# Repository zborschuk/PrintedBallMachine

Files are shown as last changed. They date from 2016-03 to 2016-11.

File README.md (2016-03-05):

# PrintedBallMachine
A 3d Printed ball machine, hung on pegboard.

The goal of this repo is to demonstrate the specifications of a printed ball machine, composed of interchangeable modules.

Therefore, the biggest component is the ruleset.

The inlet hopper is given as a standalone STL, for use with other graphics programs, as well as the outlets.

Marbles are 5/8" steel ball bearings.  Steel is heavy.

Inlets align on the 1" marks, outlets on the 1/2"; your machine may raise or lower marbles by any 1" increment.  The centerline for all inlets and outlets is 1" from the start of the hanger.

The easiest module is the simple slope, which is included.  I'll be working on a lifter or two next, and will continue to add modules.

Paul

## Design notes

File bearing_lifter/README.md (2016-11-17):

# Bearing Lifter
This is a lifter module, utilizing a print-in-place bearing.

Mechanical Parts:
1 motors
2 M5 screws and nuts for the handle
4 M3 screws to attach the motor
1 M3 screw to attach the guard

Parts to Print:
1 * bl_inlet.stl
1 * bl_outlet.stl
1 * bl_lift_gear.stl
1 * bl_drive_gear.stl
1 * bl_spiral.stl
1 * bl_guard.stl

Standard Parts
2 * stand.stl
1 * handle.stl
1 * breturn_inlet.stl
1 * breturn_outlet.stl
2 * breturn_peg.stl
4 * peg_1x.stl
1 * peg_2x.stl
6 * peg_3x.stl

Notes:
Motor direction matters!
bl_inlet uses long pegs where it can.
You need a sideways support peg for the bl_outlet, under the fang-like curve.

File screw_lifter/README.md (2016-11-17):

# Screw Lifter
This is a lifter module, utilizing two separate screw lifters and a spiral drop.

Mechanical Parts:
2 motors
2 M5 screws and nuts for the handle

Parts to Print:
2 * sl_inlet.stl
2 * sl_screw_2s.stl
1 * sl_bowl_drop.stl
1 * sl_bowl_catch.stl

Standard Parts
2 * stand.stl
1 * handle.stl
1 * breturn_inlet.stl
1 * breturn_outlet.stl
2 * breturn_peg.stl
4 * peg_1x.stl
2 * peg_2x.stl
4 * peg_3x.stl
1 * insert_peg.stl

Notes:
Motor direction matters!
sl_inlet uses long pegs where it can.
sl_bowl_catch.stl needs an insert peg on its outlet.

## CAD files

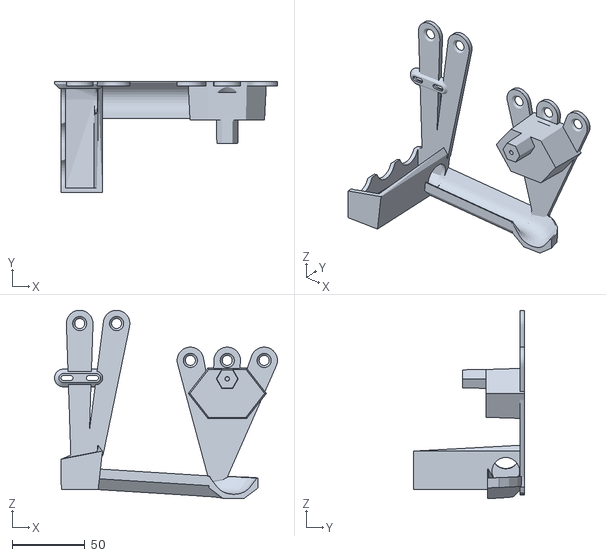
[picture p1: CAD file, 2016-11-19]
bearing_lifter/bl_inlet.stl
153.5 x 76.3 x 129.7

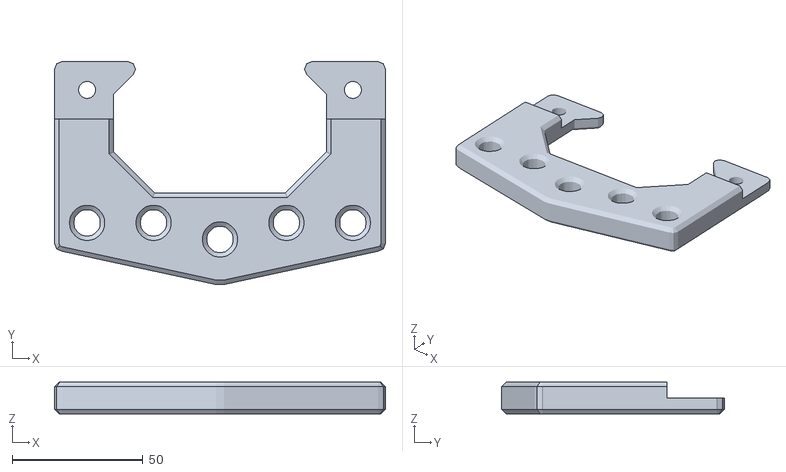
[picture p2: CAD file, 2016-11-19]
bearing_lifter/handle.stl
126.5 x 85.2 x 12.2

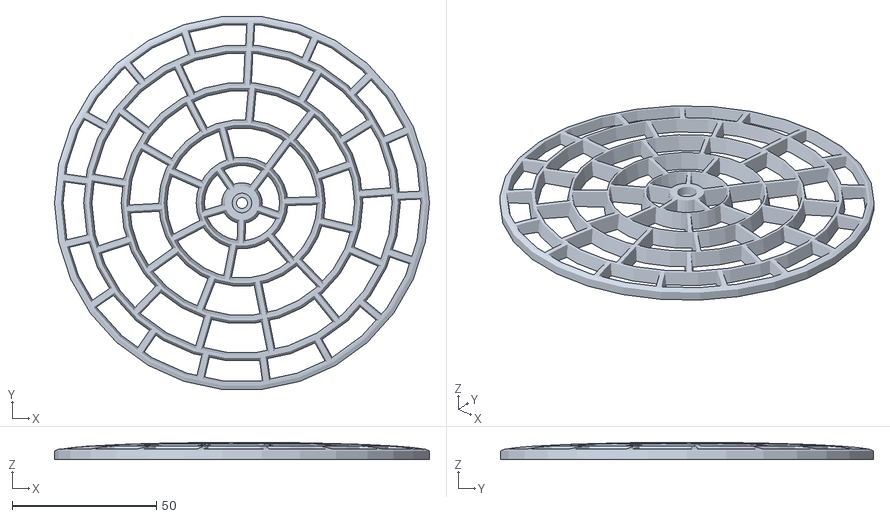
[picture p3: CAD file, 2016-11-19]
bearing_lifter/bl_guard.stl
130.0 x 129.3 x 5.98

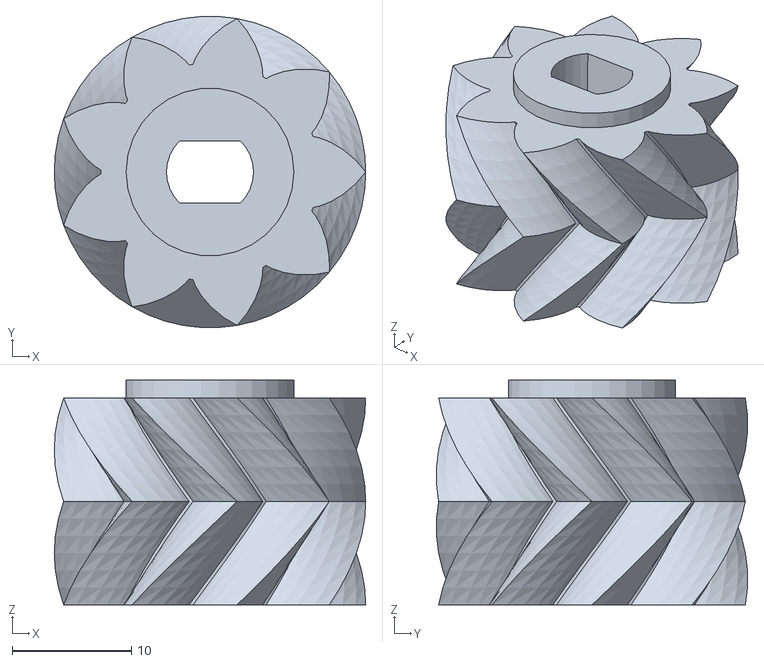
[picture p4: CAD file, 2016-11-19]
bearing_lifter/bl_drive_gear.stl
26.2 x 26.1 x 18.9

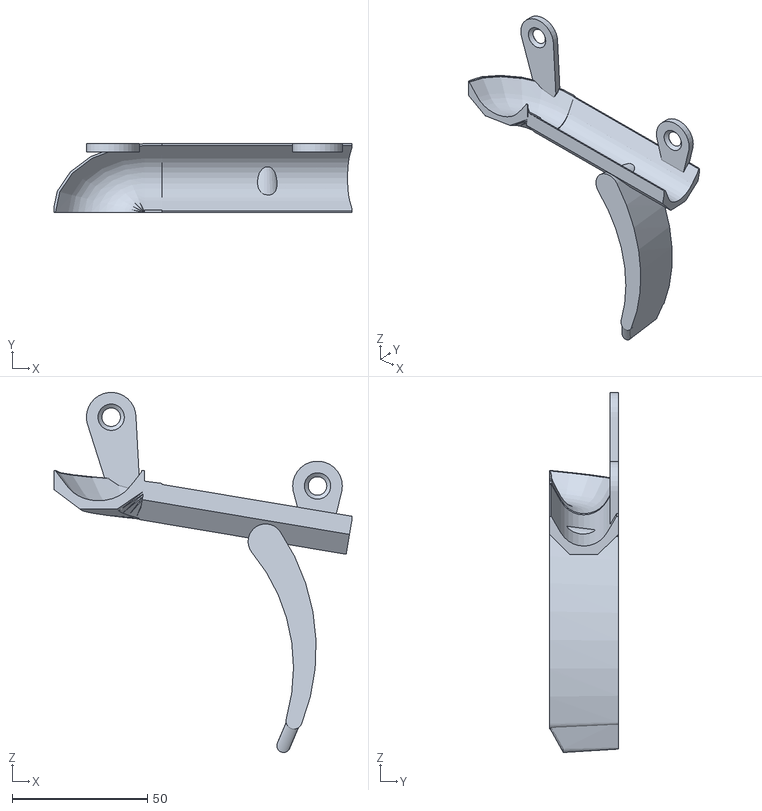
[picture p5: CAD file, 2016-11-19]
bearing_lifter/bl_outlet.stl
110.0 x 25.5 x 133.0

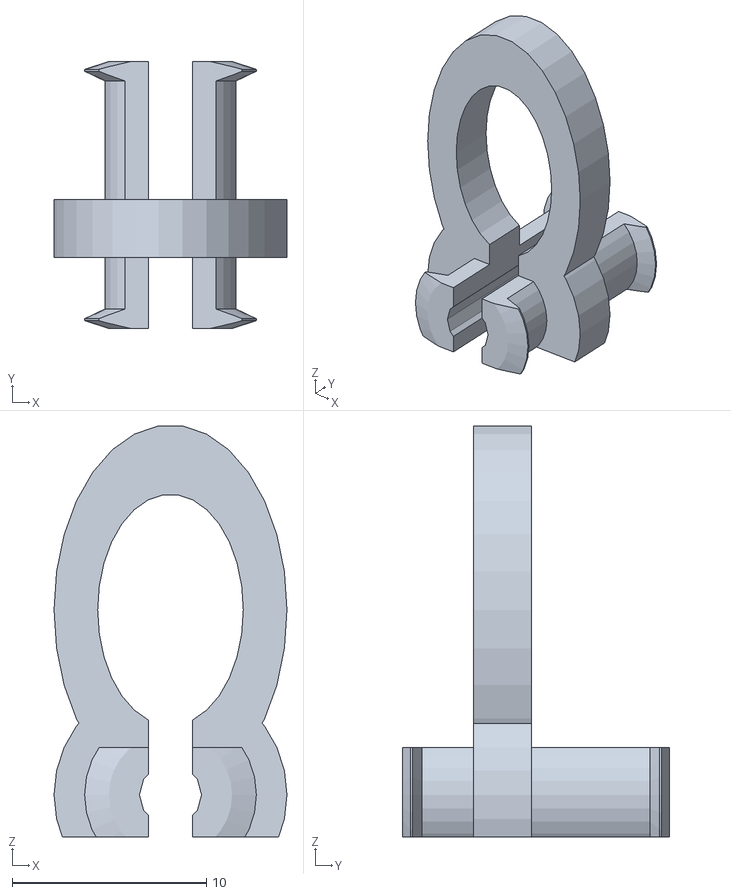
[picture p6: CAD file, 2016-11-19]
bearing_lifter/insert_peg.stl
12.0 x 13.8 x 21.2

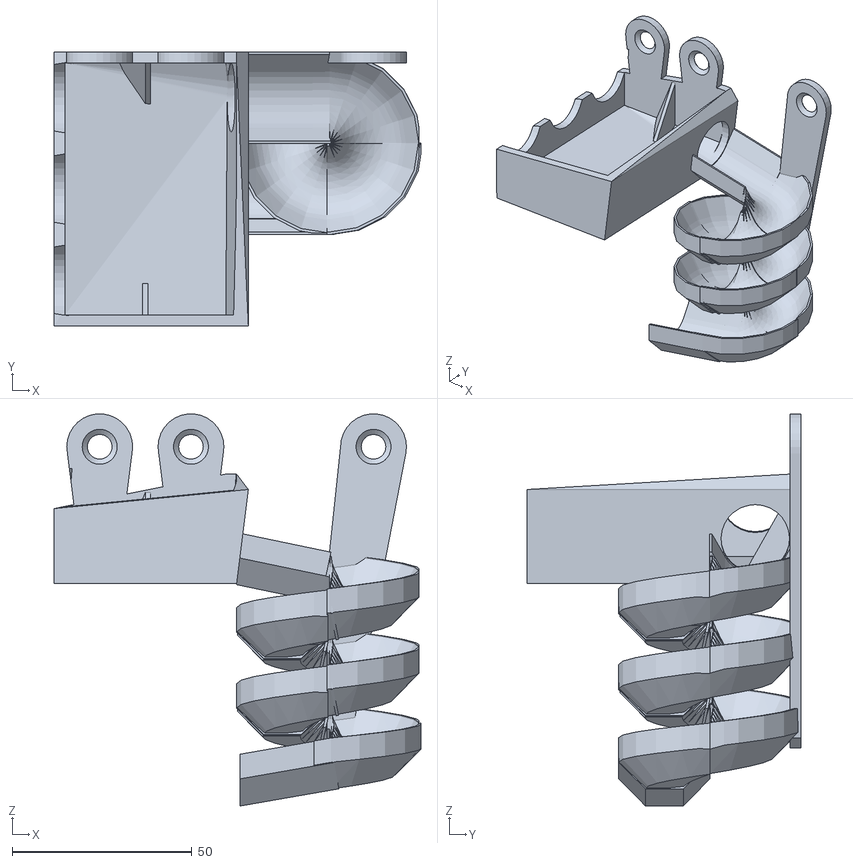
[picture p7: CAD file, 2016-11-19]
bearing_lifter/bl_spiral.stl
102.1 x 76.2 x 109.1

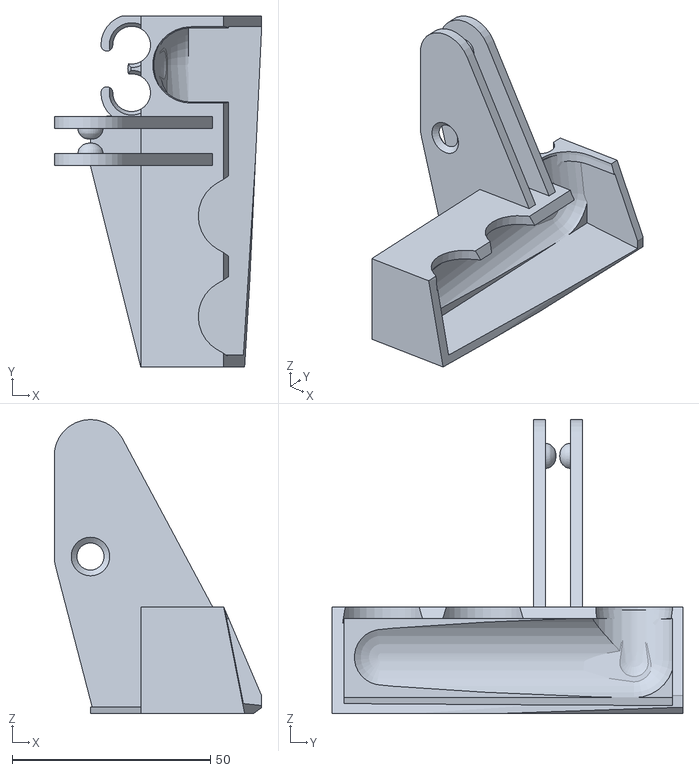
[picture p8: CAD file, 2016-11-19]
bearing_lifter/breturn_inlet.stl
52.3 x 88.5 x 74.2

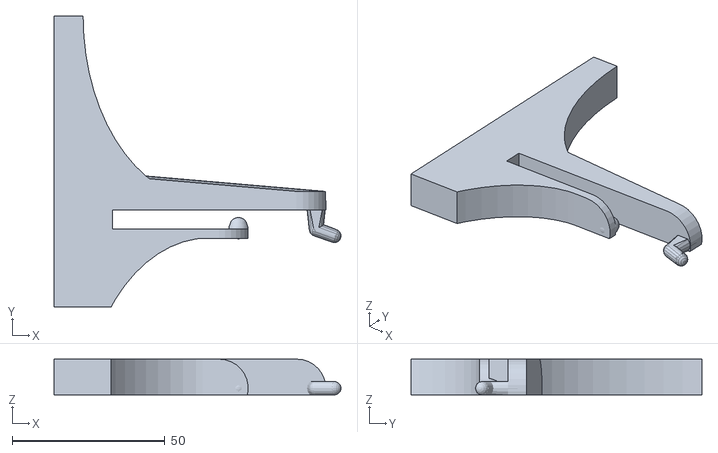
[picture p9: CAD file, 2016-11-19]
bearing_lifter/stand.stl
93.8 x 95.1 x 11.7

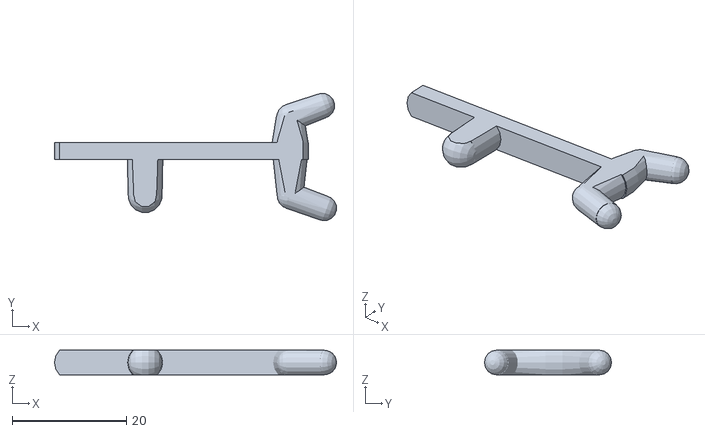
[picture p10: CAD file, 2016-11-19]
bearing_lifter/peg_1x.stl
49.4 x 22.3 x 4.35

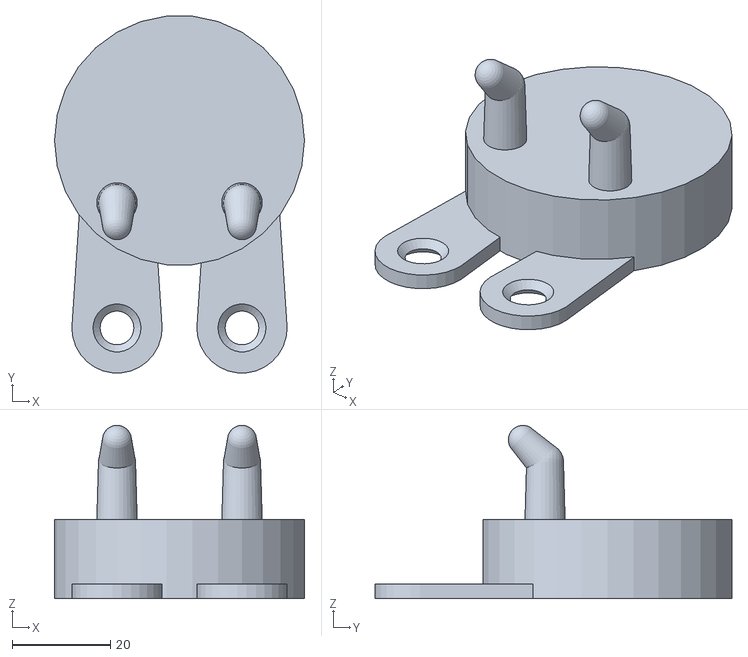
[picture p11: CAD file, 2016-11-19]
bearing_lifter/handle_mount.stl
50.8 x 72.5 x 35.2

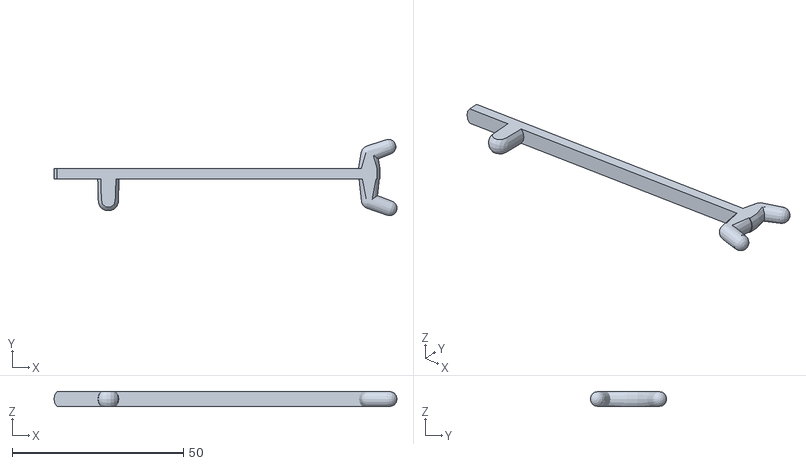
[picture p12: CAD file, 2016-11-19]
bearing_lifter/peg_3x.stl
100.2 x 22.3 x 4.35

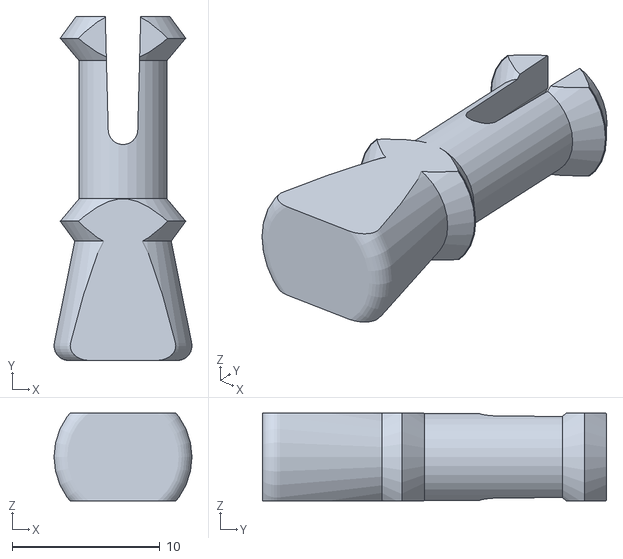
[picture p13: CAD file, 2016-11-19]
bearing_lifter/breturn_peg.stl
9.35 x 23.3 x 5.95

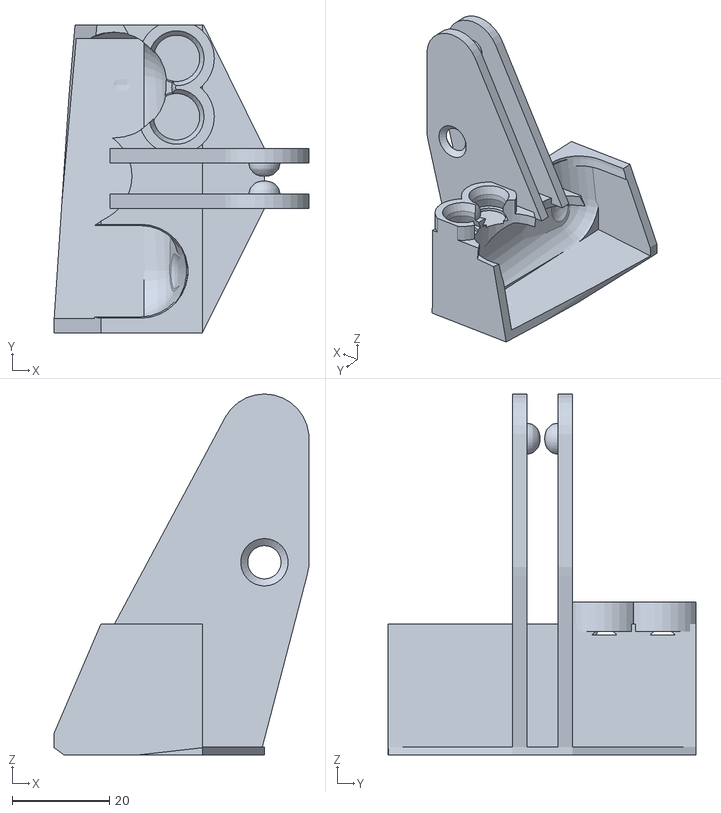
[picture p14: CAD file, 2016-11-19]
bearing_lifter/breturn_outlet.stl
52.3 x 63.3 x 74.2

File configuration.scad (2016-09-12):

in = 25.4;

$fn=30;

slop = .2;

//pegboard variables
peg_rad = 1/4*in/2;
peg_sep = 1*in;
peg_thick = 1/4*in;

wall=3;

//used for the ball return
dowel_rad = (3/8)/2*in;

//ball variables
ball_rad = 5/8*in/2;

//track_rad = ball_rad+1+.5;  //this is the minimum size, I think
track_rad = in/2-wall; //this makes the track an inch wide

//inlet variables
inlet_x = in;
inlet_y = in*2;
inlet_z = in*1;
INLET_HOLE = 1;
INLET_SLOT = 2;
INLET_NONE=0;
NONE = 0;
NORMAL = 0;
REVERSE = 5;
SWITCH = 8;
FLIP_FLOP = 9;

PEG_PIN = 1;
PEG_HOOK = 2;
PEG_NONE = 0;

m3_rad = 3/2 + slop;
m3_cap_rad = 6/2 + slop;

//pin variables
pin_tolerance = .25;
pin_rad = 4;
pin_lt = 1;

//motor shaft variables
motor_dflat=.9;
motor_shaft=7+slop/4;
motor_bump=1.5;

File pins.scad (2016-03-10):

// Pin Connectors V3
// Tony Buser <tbuser@gmail.com>
// Modified by Emmett Lalish

object=0;//[0:pin,1:pinpeg,2:pinhole]
length=20;
diameter=8;
//Only affects pinhole
hole_twist=0;//[0:free,1:fixed]
//Only affects pinhole
hole_friction=0;//[0:loose,1:tight]
//Radial gap to help pins fit into tight holes
pin_tolerance=0.2;
//Extra gap to make loose hole
loose=0.3;
lip_height=3;
lip_thickness=1;
hf=hole_friction==0 ? false : true;
ht=hole_twist==0 ? false : true;

if(object==0)pin(h=length,r=diameter/2,lh=lip_height,lt=lip_thickness,t=pin_tolerance);
if(object==1)pinpeg(h=length,r=diameter/2,lh=lip_height,lt=lip_thickness,t=pin_tolerance);
if(object==2)pinhole(h=length,r=diameter/2,lh=lip_height,lt=lip_thickness,t=loose,
	tight=hf,fixed=ht);

module test() {
  tolerance = 0.3;
  
  translate([-12, 12, 0]) pinpeg(h=20);
  translate([12, 12, 0]) pintack(h=10);
  
  difference() {
    union() {
      translate([0, -12, 2.5]) cube(size = [59, 20, 5], center = true);
      translate([24, -12, 7.5]) cube(size = [12, 20, 15], center = true);
    }
    translate([-24, -12, 0]) pinhole(h=5, t=tolerance);
    translate([-12, -12, 0]) pinhole(h=5, t=tolerance, tight=false);
    translate([0, -12, 0]) pinhole(h=10, t=tolerance);
    translate([12, -12, 0]) pinhole(h=10, t=tolerance, tight=false);
    translate([24, -12, 15]) rotate([0, 180, 0]) pinhole(h=10, t=tolerance);
  }
}

module pinhole(h=10, r=4, lh=3, lt=1, t=0.3, tight=true, fixed=false) {
  // h = shaft height
  // r = shaft radius
  // lh = lip height
  // lt = lip thickness
  // t = extra tolerance for loose fit
  // tight = set to false if you want a joint that spins easily
  // fixed = set to true so pins can't spin
  
intersection(){
  union() {
	if (tight == true || fixed == true) {
      pin_solid(h, r, lh, lt);
	  translate([0,0,-t/2])cylinder(h=h+t, r=r, $fn=30);
	} else {
	  pin_solid(h, r+t/2, lh, lt);
	  translate([0,0,-t/2])cylinder(h=h+t, r=r+t/2, $fn=30);
	}
    
    
    // widen the entrance hole to make insertion easier
    //translate([0, 0, -0.1]) cylinder(h=lh/3, r2=r, r1=r+(t/2)+(lt/2),$fn=30);
  }
  if (fixed == true) {
	translate([-r*2, -r*0.75, -1])cube([r*4, r*1.5, h+2]);
  }
}}

module pin(h=10, r=4, lh=3, lt=1, t=0.2, side=false) {
  // h = shaft height
  // r = shaft radius
  // lh = lip height
  // lt = lip thickness
  // side = set to true if you want it printed horizontally

  if (side) {
    pin_horizontal(h, r, lh, lt, t);
  } else {
    pin_vertical(h, r, lh, lt, t);
  }
}

module pintack(h=10, r=4, lh=3, lt=1, t=0.2, bh=3, br=8.75) {
  // bh = base_height
  // br = base_radius
  
  union() {
    cylinder(h=bh, r=br);
    translate([0, 0, bh]) pin(h, r, lh, lt, t);
  }
}

module pinpeg(h=20, r=4, lh=3, lt=1, t=0.2) {
  union() {
    translate([0,-0.05, 0]) pin(h/2+0.1, r, lh, lt, t, side=true);
    translate([0,0.05, 0]) rotate([0, 0, 180]) pin(h/2+0.1, r, lh, lt, t, side=true);
  }
}

// just call pin instead, I made this module because it was easier to do the rotation option this way
// since openscad complains of recursion if I did it all in one module
module pin_vertical(h=10, r=4, lh=3, lt=1, t=0.2, cut=false) {
  // h = shaft height
  // r = shaft radius
  // lh = lip height
  // lt = lip thickness

  difference() {
    pin_solid(h, r-t/2, lh, lt);
    
    // center cut
    translate([-lt*3/2, -(r*2+lt*2)/2, h/5+lt*3/2]) cube([lt*3, r*2+lt*2, h]);
    //translate([0, 0, h/4]) cylinder(h=h+lh, r=r/2.5, $fn=20);
    // center curve
    translate([0, 0, h/5+lt*3/2]) rotate([90, 0, 0]) cylinder(h=r*2, r=lt*3/2, center=true, $fn=20);
  
    // side cuts
    if(cut==true){
        translate([-r*2, -r-r*0.75+t/2, -1]) cube([r*4, r, h+2]);
        translate([-r*2, r*0.75-t/2, -1]) cube([r*4, r, h+2]);
    }
  }
}

// call pin with side=true instead of this
module pin_horizontal(h=10, r=4, lh=3, lt=1, t=0.2) {
  // h = shaft height
  // r = shaft radius
  // lh = lip height
  // lt = lip thickness
  translate([0, 0, r*0.75-t/2]) rotate([-90, 0, 0]) pin_vertical(h, r, lh, lt, t);
}

// this is mainly to make the pinhole module easier
module pin_solid(h=10, r=4, lh=3, lt=1) {
  union() {
    // shaft
    cylinder(h=h-lh, r=r, $fn=30);
    // lip
    // translate([0, 0, h-lh]) cylinder(h=lh*0.25, r1=r, r2=r+(lt/2), $fn=30);
    // translate([0, 0, h-lh+lh*0.25]) cylinder(h=lh*0.25, r2=r, r1=r+(lt/2), $fn=30);
    // translate([0, 0, h-lh+lh*0.50]) cylinder(h=lh*0.50, r1=r, r2=r-(lt/2), $fn=30);

    // translate([0, 0, h-lh]) cylinder(h=lh*0.50, r1=r, r2=r+(lt/2), $fn=30);
    // translate([0, 0, h-lh+lh*0.50]) cylinder(h=lh*0.50, r1=r+(lt/2), r2=r-(lt/3), $fn=30);    

    translate([0, 0, h-lh]) cylinder(h=lh*0.25, r1=r, r2=r+(lt/2), $fn=30);
    translate([0, 0, h-lh+lh*0.25]) cylinder(h=lh*0.25, r=r+(lt/2), $fn=30);    
    translate([0, 0, h-lh+lh*0.50]) cylinder(h=lh*0.50, r1=r+(lt/2), r2=r-(lt/2), $fn=30);    

    // translate([0, 0, h-lh]) cylinder(h=lh, r1=r+(lt/2), r2=1, $fn=30);
    // translate([0, 0, h-lh-lt/2]) cylinder(h=lt/2, r1=r, r2=r+(lt/2), $fn=30);
  }
}

module pinshaft(h=10, r=4, t=0.2, side=false){
flip=side ? 1 : 0;
translate(flip*[0,h/2,r*0.75-t/2])rotate(flip*[90,0,0])
intersection(){
	cylinder(h=h, r=r-t/2, $fn=30);
	translate([-r*2, -r*0.75+t/2, -1])cube([r*4, r*1.5-t, h+2]);
}
}

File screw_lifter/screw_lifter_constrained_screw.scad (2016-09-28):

include <../configuration.scad>;
use <../base.scad>;

part = 10;

screw_rad = ball_rad+wall*2;
screw_pitch = ball_rad*2+wall*2;
screw_offset = -wall-screw_rad-.9;
screw_length = 4.6;

//next section
%translate([in*12,0,in*10]) inlet();

%translate([in*4, 0, in*1]) offset_slope_module();

//laid out for printing
if(part == 0)
    screw_inlet();
if(part == 1)
    screw_segment(length=screw_length, starts=2, top=ROUND);
if(part == 2)
    screw_segment(length=screw_length, starts=1, top=ROUND);
if(part == 3)
    screw_outlet();
if(part == 4)
    screw_guide();


if(part==10){
    assembled();
}

angle = 0;

//tops for the lift screws
ROUND = 2;
NONE = 0;
PEG = 1;

module assembled(){

    %pegboard([12,12]);
    %translate([peg_sep*3.8,-ball_rad,peg_sep*3.2]) sphere(r=ball_rad);
    
    screw_inlet();
    
    translate([peg_sep*2,screw_offset,0]) rotate([0,angle,90]) translate([0,0,0]) screw_segment(length=screw_length, starts=2, top=ROUND);
    //translate([peg_sep*2,screw_offset,0]) rotate([0,angle,0]) translate([0,0,3*screw_pitch+2]) screw_segment();
    //translate([peg_sep*2,screw_offset,0]) rotate([0,angle,0]) translate([0,0,7*screw_pitch]) screw_segment();
    
    translate([peg_sep*9,0,peg_sep*7]) screw_outlet();
}

module screw_outlet(){
    
    difference(){
        union(){
            inlet(length=3, inset=0);
        }
        
        //angled hole for the screw
        translate([0,screw_offset, 0]) hull() {
            translate([0,0,-peg_sep/2]) cylinder(r=screw_rad+1, h=100);
            rotate([0,30,0]) translate([0,0,-peg_sep]) cylinder(r=screw_rad+1, h=100);
            rotate([0,60,0]) translate([0,0,-peg_sep]) cylinder(r=screw_rad+1, h=100);
        }
    }
}

module slide_motor_mount(angle_inset = 20, max_angle = 75, motor_width = 20){
    
    zip_width = 3;
    zip_length = 5;
    
    sweep_angle = max_angle + 5;
    rad = angle_inset + motor_width+zip_width*4;
    
    difference(){
        //body
        intersection(){
            rotate([90,0,0]) cylinder(r=rad, h=wall);
            translate([-50,0,-50]) cube([100,100,100], center=true);
            rotate([0,90-sweep_angle,0]) translate([-50,0,-50]) cube([100,100,100], center=true);
        }
        
        //slots for zip ties to attach the motor
        for(i=[5:360/100:max_angle-zip_width]) rotate([0,-i,0])  {
            translate([-angle_inset,0,0]) cube([zip_width, wall*3, zip_length], center=true);
            translate([-angle_inset-motor_width-zip_width,0,0]) cube([zip_width, wall*3, zip_length], center=true);
        }
    }
}


module screw_inlet(){
    motor_width = 20;
    open_angle=0;
    
    difference(){
        union(){
            inlet(length=3, inset=0, outlet=NONE, hanger_height=2);
            
            //motor hangs under the inlet, with an adustable angle centered on the hole in the floor.
            %translate([peg_sep*2,screw_offset,0]) rotate([0,-90+angle,0]) rotate([0,90,0]) rotate([0,0,-90]) translate([0,0,-21]) motor_holes();
            
            //the motor mount uses a zip tie to hold the motor in, allowing it to pivot to angle the screw a bit.
            *translate([peg_sep*2.5,0,-.1]) slide_motor_mount(angle_inset = 30);
            
            //guide track
           translate([in*2,in/2+screw_offset,0]) for(i=[0,1]) mirror([i,0,0]) rotate([0,0,open_angle]) translate([screw_rad+ball_rad+wall*1.5,0,0]) rotate([0,-90,0]) track(rise = 0, run = in*(4+i));
            
            //balls
            *translate([in*3-ball_rad-wall,screw_offset,in*3+10]) sphere(r=ball_rad);
           
           //false floor
           mirror([0,1,0]) cube([in*3, in*3, in/2+1]);
           
           //top exit track
           translate([in*1.25,in/2+screw_offset+in*.15,in*4]) scale([1,1.3,1]) {
               track(rise = -in/4, run = in*3);
               hull(){
                   translate([in*.75, -track_rad-wall, track_rad/2]) cube([in*1.5, track_rad*2+wall*2, track_rad], center=true);
                   translate([in*.75, -track_rad-wall, -track_rad*1.5]) cube([in*1.5, track_rad*2, track_rad], center=true);
               }
           }
        }
        
        //top exit track hollow
        translate([in*1.5,in/2+screw_offset+in*.15,in*4]) scale([1,1.3,1]) track(rise = -in/4, run = in*3, solid=-1);
        
        //guide track hollow
           translate([in*2,screw_offset,wall*2]) hull() for(i=[0,1]) mirror([i,0,0]) rotate([0,0,open_angle]) translate([screw_rad-2.3,0,0]) {
               //track(rise = 0, run = in*4.5, solid=-1);
               cylinder(r=ball_rad+wall, h=in*4.5);
           }
               
           //cube cut
           translate([100+in*4-1,0,100]) cube([200,200,200], center=true);
        
        
        //ball entry to the guides
        translate([in*2,screw_offset,ball_rad+wall*2]) for(i=[0,1]) mirror([i,0,0]) translate([screw_rad,0,0]) {
            hull(){
                sphere(r=ball_rad+wall);
                //rotate([0,0,-15])
                translate([-screw_rad/2,-in*3-screw_offset+ball_rad+wall*2,wall*2]) sphere(r=ball_rad+wall);
            }
        }
        
        //get the ball to the guides
        hull(){
            translate([in*2,screw_offset,ball_rad+wall*2])
            translate([screw_rad/2,-in*3-screw_offset+ball_rad+wall*2,wall*2])
                #sphere(r=ball_rad+wall);
            translate([in/2,screw_offset,ball_rad+wall*2])
            translate([0,-in*3-screw_offset+ball_rad+wall*2,wall*2.5])
                #sphere(r=ball_rad+wall);
        }
        
        hull(){
            translate([in/2,screw_offset,ball_rad+wall*2])
            translate([0,-in*3-screw_offset+ball_rad+wall*2,wall*2.5])
                #sphere(r=ball_rad+wall);
            
            translate([in/2,-in/2,ball_rad+wall*5])
                #sphere(r=ball_rad+wall);
        }
        
        //motor mount
        #translate([in*2,screw_offset,0]) rotate([0,0,180]) motor_holes();
        
                
        // hole for the screw
        translate([in*2,screw_offset, 0]) hull() {
            translate([0,0,-peg_sep/2]) cylinder(r=screw_rad+.25, h=200);
            *rotate([0,30,0]) translate([0,0,-peg_sep]) cylinder(r=screw_rad+1, h=100);
            *rotate([0,60,0]) translate([0,0,-peg_sep]) cylinder(r=screw_rad+1, h=100);
        }
        
        
    }
}

//length is measured in revolutions!
module screw_segment(length = 4, starts = 2, top = PEG){  
    pitch = screw_pitch;
    true_pitch = screw_pitch*starts;
    
    screw_inner_rad = (7.5+wall)/2;
    difference(){
        union(){        
            //main tube
            cylinder(r=screw_inner_rad, h=length*pitch);
            
            //we'll need a screw, too...
            for(i=[1:starts]) rotate([0,0,i*(360/starts)]) translate([0,0,-pitch]) screw_threads(length = (length+1)*pitch, pitch = true_pitch);
            
            //handle the screw top
            if(top == PEG){
                //connect to the next screw along
                translate([0,0,length*pitch-.1]) d_slot(shaft=7.5-slop*3, height=10-slop*2, dflat=.4+.4+slop, double_d=true);
            }
            
            if(top == ROUND){
                //this is just flat for now
            }
        }
        
        //d slot for the connection
        translate([0,0,-.1]) d_slot(shaft=7.5, height=10, dflat=.4+.4, double_d=true);
        
        //flatten the base
        translate([0,0,-50]) cube([50,50,100], center=true);
    }
}

module screw_threads(length = 30, pitch = 5){
    facets = 30;
    
    inner_rad = 7;
    
    stretch = 1.1;
    
    intersection(){
        cylinder(r=screw_rad-slop, h=length);
        
        for(turn=[0:pitch:length]) translate([0,0,turn]) {
            //single ring
            for(i=[0:facets]) {
                hull(){
                    rotate([0,0,i*(360/facets)]) translate([inner_rad,0,i*pitch/facets]) scale([stretch,1,1]) rotate([90,0,0]) cylinder(r=screw_rad-slop-inner_rad, h=.1, center=true, $fn=3);
                    
                    rotate([0,0,(i+1)*360/facets]) translate([inner_rad,0,(i+1)*pitch/facets]) scale([stretch,1,1]) rotate([90,0,0]) cylinder(r=screw_rad-slop-inner_rad, h=.1, center=true, $fn=3);
                }
            }
        }
        
    }
}
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

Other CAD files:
bearing_lifter/peg_2x.stl
screw_lifter/breturn_outlet.stl
screw_lifter/sl_bowl_catch.stl
screw_lifter/sl_inlet.stl
base.scad
Loop-De-Loop.scad
ball_return/ball_return.scad
bearing_lifter/bearing_lifter.scad
chain_lifter/bearing.scad
chain_lifter/chain_lifter.scad
chain_lifter/easy_print_bearing.scad
clank_drop/clank_drop.scad
handle.scad
peg.scad
screw_drop/bowl_drop.scad
screw_drop/screw_drop.scad
screw_drop/torricelli_trumpet.scad
screw_lifter/breturn_inlet.stl
screw_lifter/breturn_peg.stl
screw_lifter/handle.stl
screw_lifter/handle_mount.stl
screw_lifter/insert_peg.stl
screw_lifter/peg_1x.stl
screw_lifter/peg_2x.stl
screw_lifter/peg_3x.stl
screw_lifter/screw_lifter.scad
screw_lifter/sl_bowl_drop.stl
screw_lifter/sl_screw_1s.stl
screw_lifter/sl_screw_2s.stl
screw_lifter/stand.stl
stair_lifter/stair_lifter.scad

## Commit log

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2016-03-05 Started to work on curved exits for the track.
    Basically, curved outlet -> rotary lifter
    [base.scad]
2016-03-05 In-progress commit
    Working on curved ends of the track. Mostly there, but the angles are eluding me... time to do some drawings.
    [base.scad]
2016-03-05 Fully working angled outputs!
    Angle can be anything from 0 to 90... we don't go any farther.
    Next step will be making a simple slope return - goes out one side, then drops down and comes back.
    Then we need a lifter, and we'll have a complete proof of concept.
    [base.scad, peg.stl, simple_slope.stl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]
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2016-03-05 Fixed up the inlet... I was doing it backwards, and didn't realize it right away.
    Now it's a bit bigger. I'm debating if it needs a bigger slope on the bottom.
    Also the bare inlet now has a hole for the marble to come out. I didn't think it should have one, but with the sloped base I thought it wise to put the hole in. I'll upload other options for the module later.
    [base.scad, bearing_lifter.scad, inlet.stl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]
2016-03-06 Finished tracks with curves in them, added reverser
    Reverser hasn't printed yet, but it will soon. Minor updates to most other parts :-)
    Paul
    [base.scad, configuration.scad, peg.stl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]
2016-03-07 First stab at a lifter.
    Uses Emmett's gear bearing, with an additional geared exterior, intended to be motor driven.
    I'll add a motor mount soon; I was hoping to find a decent motor < 1" thick, but no luck so far.
    Not sure what to do next. For the demo, I'd really like to get a closed-loop system going... maybe I should add a return path to this guy? Build another lifter, that can accept marbles from both dire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
    Already thinking that the inlet should be triple-wide by default.
    [base.scad, bearing.scad, bearing_lifter.scad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]
2016-03-07 Mirrored the gear motor inlet.
    Now you can have it accept marbles from the left or the right - perfect for making a closed-loop system.
    The parts are still printing, and I did find a thin motor - so it'll probably be Tuesday before I have a motorized system, but at least it'll be compact.
    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
    [bearing_lifter.scad, bearing_lifter_inlet_right.stl, bearing_lifter_outlet.stl]
2016-03-07 Added an offset slope
    Mainly to slow down the marbles... in the demo machine there're a lot of simple slopes, because I don't have time to do much else. Eventually they'll be replaced by cool things :-)
    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
    [base.scad, bearing_lifter.scad, offset_slope.stl]
2016-03-09 Updated pegs, bearing lifter inlet, initial commit of a drive gear
    Need to make a motor mount next... assuming the drive gear works, anyways.
    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
    [base.scad, bearing_lifter.scad, bearing_lifter_drive_gear.stl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]
2016-03-09 in-progress commit
    Working on making a motor mount for the bearing lifter.
    [base.scad, bearing.scad, bearing_lifter.scad]
2016-03-09 Moved the lifter into its own directory
    Also built a motor mount into the outlet; it allows the motor to swivel, so you can use larger drive gears if desired.
    With a 14rpm motor, 11 tooth drive gear, 71 tooth ring gear, and 19 balls per ring revolution, you get a bit over 40 marbles per minute.
    I've added a 17 tooth drive gear, which gives 63 marbles per minute :-)
    [bearing.scad, bearing_lifter.scad, bearing_lifter_drive_gear.stl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]
2016-03-10 multiple changes
    - Made the inlet more modular, so you can make a bigger one
    - Added the option for pins on the pegs
    - Started work on a stair lifter, using arm linkages.
    [base.scad, configuration.scad, pins.scad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]
2016-03-11 Working on stair lifter
    Using cams that stack up... and hopefully some threaded rod to hold all the cams on.
    Need to work out:
    guide for the baskets - probably a triangular rail, mounted to the pegboard
    different heights for the baskets
    better cam lobes - they don't look right.
    better cam follower?
    [bar.stl, base.scad, bearing_lifter.scad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]
2016-03-11 first go at the stair lifter
    Still needs an exit strategy :100:
    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
    [cam_lobe.stl, drive_shaft.stl, stair_lifter.scad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]
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2016-03-13 Updated the inlet - fins!
    Base Inlet is more modular, bearing lifter got some tweaks to the inlet.
    Added a catch basin - for gravity or straight-through machines.
    Added a screw drop - it's cool.
    Updated the reverser, because my closed loop was a little too wide for the scavenged bit of pegboard I've been using.
    [base.scad, catch_basin.stl, inlet.stl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]
2016-03-23 Added the handles.
    The holes are 1/4" separated - so you can fine-tune the height a bit for hanging.
    [handle.scad, handle.stl]
2016-03-24 Moved one of the hangers on the screw drop - should shake a bit less.
    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
    [screw_drop.scad, screw_drop.stl]
2016-03-26 Broke the pegs into their own file, and added a ball-return peg.
    For long runs, the ball-return is intended to mate with five 3/8"
    dowels to move the marbles back to the start.
    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
    [ball_return_peg.stl, base.scad, configuration.scad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]
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2016-05-02 Slight changes to the hook.
    The offset hook didn't seem promising. This one at least can get driven by a simple shape; next step is to make a driver, probably a hexagon bearing. I have different motors coming, plan to make some universal drivers.
    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
    [chain_lifter.scad]
2016-05-09 Modified the gear lifter to accommodate new motors.
    Specifically these motors: https://www.pololu.com/product/1120
    Pololu plastic gear motors. The other main difference is that they run at 5v instead of 12v.
    They're a bit fast at 5v, but not obnoxiously so; makes the printed ball machine a bit more chaotic.
    Roughly 45 rotations per minute.
    These motors work much better than the super-thin guys - it's night and day. Plus, they're cheap and from a reliable source!
    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
    [bearing_lifter.scad, bearing_lifter_drive_gear.stl, bearing_lifter_inlet.stl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]
2016-05-16 Fixing up the lifter a little.
    Need something to tide me over while I work on other projects.
    [bearing_lifter.scad, bearing_lifter_inlet.stl]
2016-05-17 Added more gears, and loosener slots to all gears.
    [bearing_lifter.scad]
2016-05-31 Moving to triple-wide modules... and playing with the offset slope
    I think I need to move the offset to have proper turns - the angle is too great otherwise.
    [base.scad]
2016-06-01 Fixed bearing lifter gears, working on chain lifter.
    The gear now has more planets, so that it can be loose (printable) but still stable. Also added slots so I could snap the planets free with a screwdriver.
    Then working on the chain lifter a bit.
    [base.scad, bearing_lifter.scad, bearing_lifter_drive_gear.stl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]
2016-06-01 chain lifter inlet designed.
    Also moved some functions around - more modules into the base.scad, for the motor mount/d-shaft.
    Need to design the top for the chain lifter; some sort of fancy runoff? The lifter is intentionally narrow, so should be relatively straight forwards.
    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
    [base.scad, bearing_lifter.scad, chain_lifter.scad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]
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2016-06-07 More chain mods. Chain works now, at least in theory - need to design its upper portion, then print more links.
    [chain_lifter.scad, cl_drive_gear.stl, cl_idler_gear.stl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]
2016-06-07 Idler bearing finished - gotta make the outlet, and then test the lifter.
    [chain_lifter.scad, easy_print_bearing.scad]
2016-06-09 Changed to the gear bearing - the rollers didn't work at all.
    [bearing.scad, chain_lifter.scad]
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2016-06-28 Longer pegs, modularizing.
    I'm working up a single-shot module - a lifter that can recirculate OR pass marbles on - so you can easily print a single panel, or make 100 and they'll still link up.
    This will be a requirement for lifters going forwards - that they can be modified to accept marbles on the left, and deposit them on the right at the same height.
    Remaining work is to make the spiral drop go straight down - which will let you swap from return to pass on easily.
    Bonus points: a switch so you can choose recirculate/pass on at will.
    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
    [base.scad, bearing_lifter.scad, configuration.scad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]
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2016-06-29 Working on the closed-loop bearing lifter.
    Right now, to close/open the loop you need to swap out a ramp. Ideally, I'll make an actual switch, but this ought to work for now.
    Also, the screw drop needs his hanger fixed.
    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
    [base.scad, bearing_lifter.scad, bl_drive_gear.stl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]
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2016-07-01 Switcher is almost there.
    Switcher now takes a bearing, so it can become a flip-flip.
    Added a bowl drop, trumpet drop.
    [base.scad, bearing_lifter.scad, bl_drive_gear.stl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]
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2016-10-12 Updated the screw lifter; it doesn't sequester balls anymore.
    [clank_drop.scad, screw_drop.scad, screw_drop_1.stl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]
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
